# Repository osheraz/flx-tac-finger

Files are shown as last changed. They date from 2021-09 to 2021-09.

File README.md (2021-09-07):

# FlX Finger 

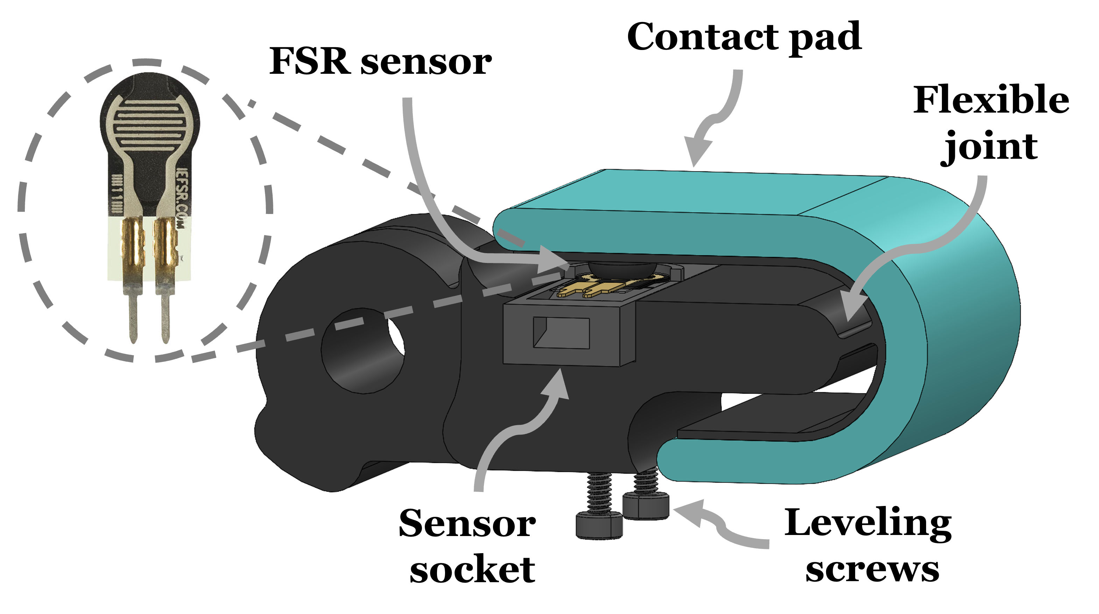
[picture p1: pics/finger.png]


This page provides instructions and design files for manufacturing the FlX finger.

## Background
FlX finger is a low-cost tactile finger. FlX finger is mostly fabricated through 3D printing and is based on the design of the distal finger link of the Model-T42 hand [1]. The FlX finger is composed of four parts seen in the figure above: finger body, contact pad, Force Sensitive Resistor (FSR) sensor and sensor socket. The finger body is connected to the contact pad solely through a flexible joint. In addition, the sensor socket with the FSR are positioned fixed to the finger body. At such configuration, the FSR is in contact with a small bulge on the back side of the contact pad.

## Force Sensitive Resistor (FSR)

FSR sensors are made of polymer films that vary their electrical resistance upon changing pressure on their surface. They are simple to use and low-cost. When an object is being pressed against the contact pad, the flexible joint and pad deform such that different contact locations across the pad provide different voltage. Pressure on the contact pad, therefore, provides voltage signals that embed information regarding the location and magnitude of contact. 

# Manufacture

## Required Materials
### Design files
1. FingerBody.stl
2. SensorSocket.stl

### Electrical
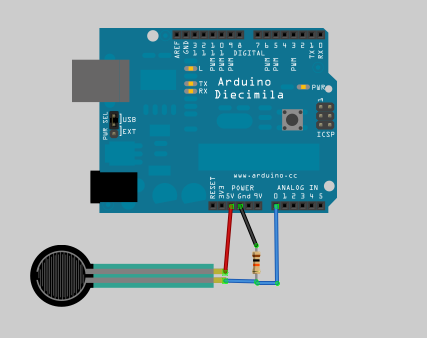
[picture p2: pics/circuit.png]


1. Arduino Uno\Nano or any equivalent board  
2. FSR 400 short by interlink electronics       
3. 4.7 kΩ resistor   
4. Wires
5. USB Cable
6. 2-Pin Female cable

### Chemicals
1.  Smooth-On Mold Star / Silicones, Inc. XP-565  or any related
2.  Ease Release 200 (not mandatory)

##  Procedure
All design files can be found in `cad` repo.\
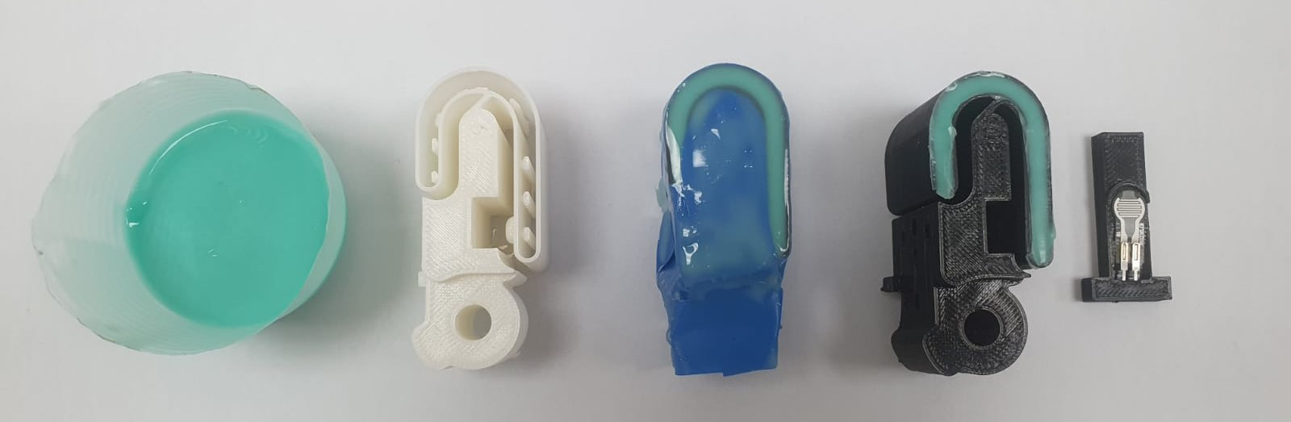
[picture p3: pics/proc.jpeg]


1. **Print parts**: Print `FingerBody.stl` and `SensorSocket.stl` in PLA using 3D printer. 
2. **Mix silicone** : Mix your silicone according to the manufacturer requirements, we used Smooth-On's silicone, which are easy to use without any vacuum degassing requirement. Mix enough Mold Star silicone ( equal amount A:B) to fill the shell of the `FingerBody`.
3. **Pour silicone**: slowly pour the silicone into the shell of the `FingerBody`. Let the silicone rest for approximtly 3 hours.
4.  **Wall removal**: Carefully remove the thin-walled molds of the  `FingerBody` using a small utility knife.
5. **Glue FSR**: Position& glue the FSR 400 short into the  `SensorSocket`.
6. **Attach insert**: Attach M2 heat insert at the bottom of the  `FingerBody` .
7.  **Wire**: Wire the FSR sensor to an analog pin of the Arduino Nano through a voltage divider of 4.7k$\Omega$ resistor.

# Test
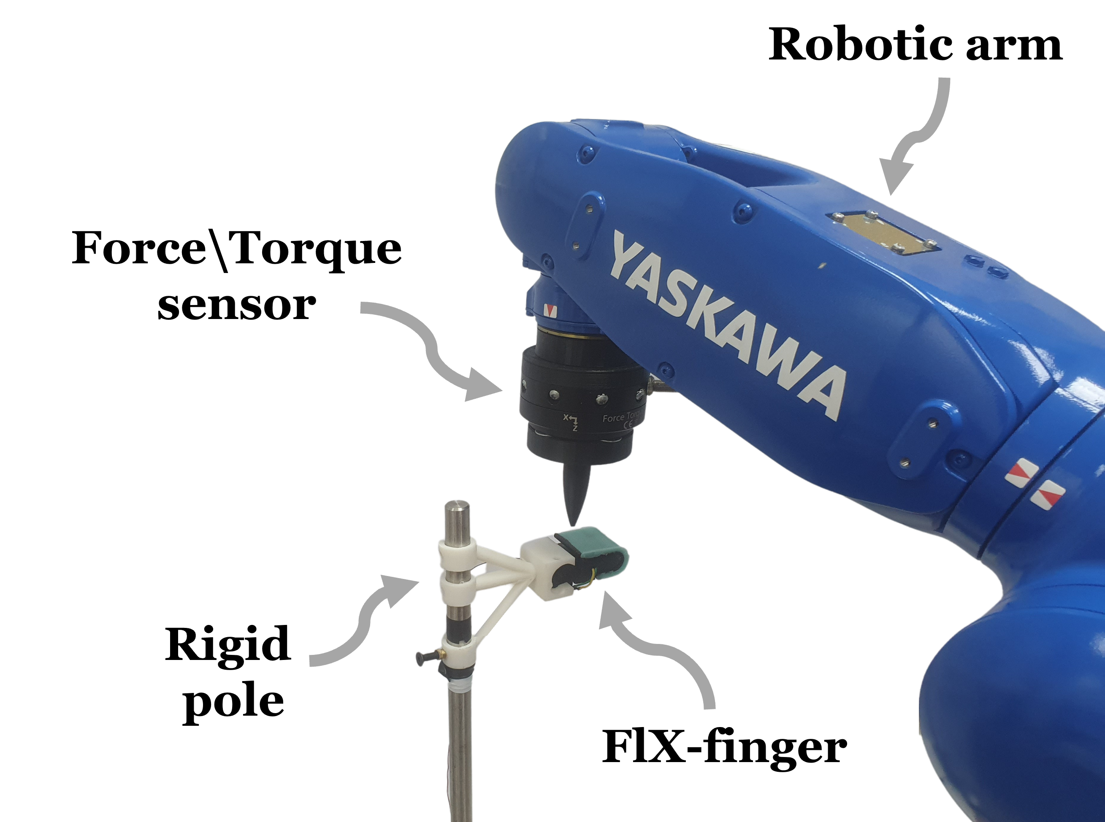
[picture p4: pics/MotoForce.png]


We tested the characteristic force distribution of the FlX finger, we have designed an experiment using a six degrees-of-freedom robotic arm equipped with a Force/Torque sensor and a rigid pole at its tip. During the experiment, the pole was pushed against the finger with predefined forces between 0-10 (N) and at 50 equal length locations along the contact pad. Results for FlX finger with initial voltage of 200 (mV) are seen in `test` repo. 
To acquire somewhat repeatability of measurements, leveling screws on the back side of the finger body are used to vary the height of the sensor socket and, thus, tune the initial voltage on the FSR. By standard, we tune the initial voltage with a weight of 100 grams directly placed on the contact pad when in an horizontal posture.

## Reference

[1] Ma, R., & Dollar, A. (2017). Yale OpenHand Project: Optimizing Open-Source Hand Designs for Ease of Fabrication and Adoption. _IEEE Robotics & Automation Magazine, 24_, 32-40.

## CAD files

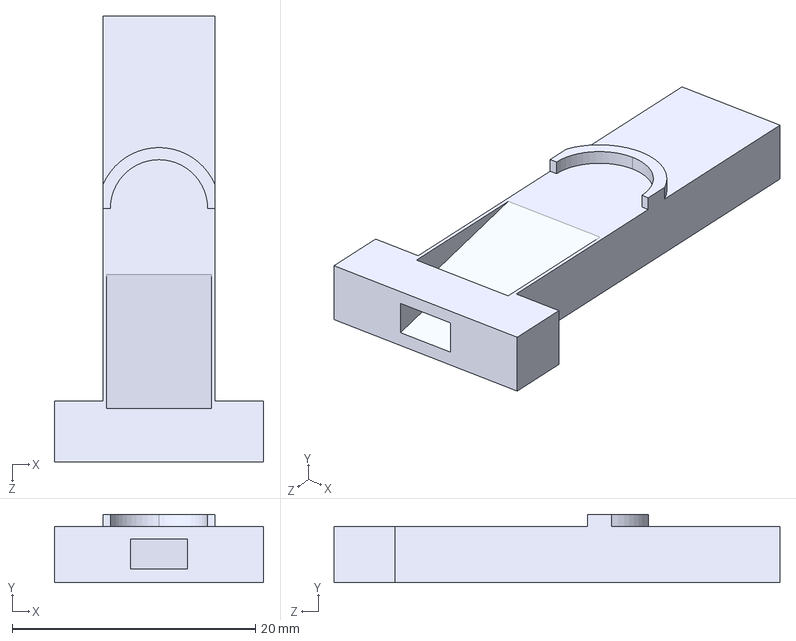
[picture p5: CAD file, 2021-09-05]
cads/SensorSocket.STEP
17.2 x 5.60 x 36.7 mm

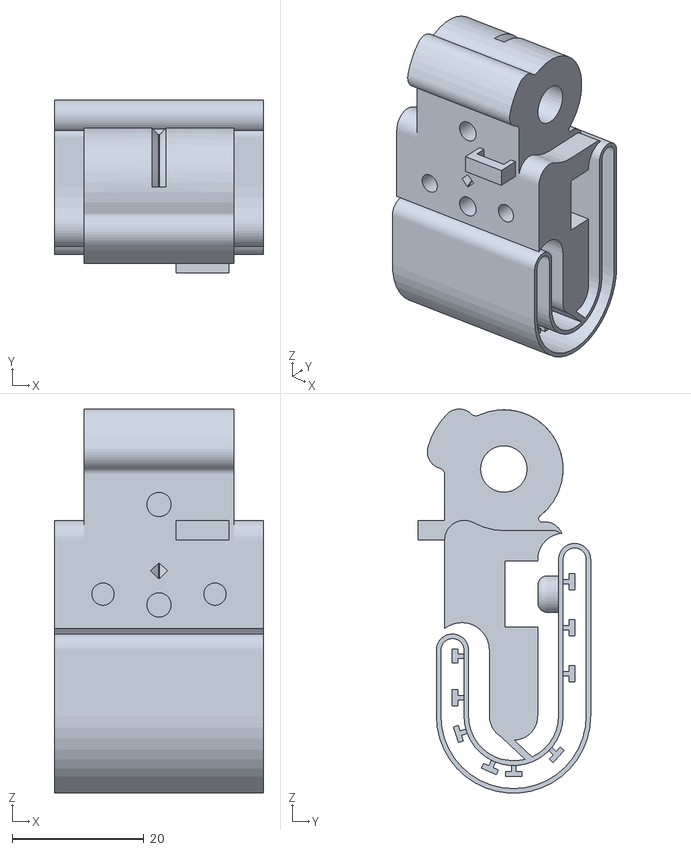
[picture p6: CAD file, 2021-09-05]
cads/FingerBody.STL
31.8 x 26.2 x 58.3

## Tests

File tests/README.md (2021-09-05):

# Signal distribution characterization
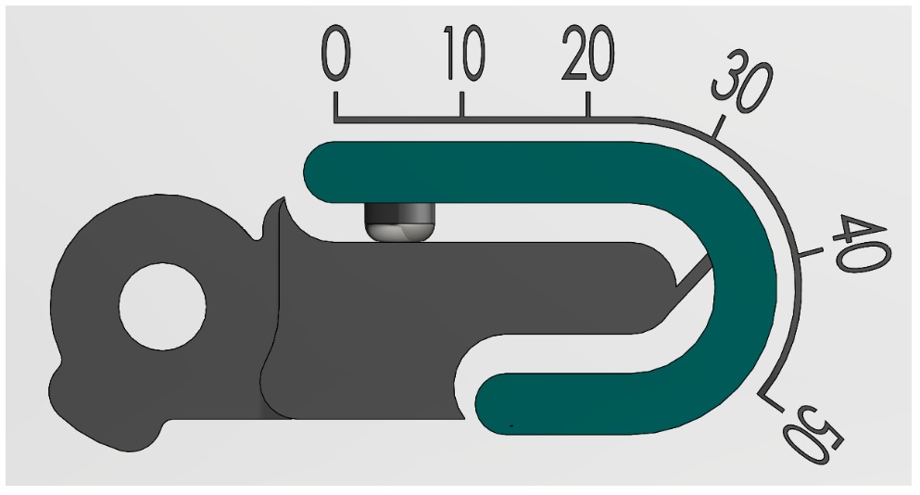
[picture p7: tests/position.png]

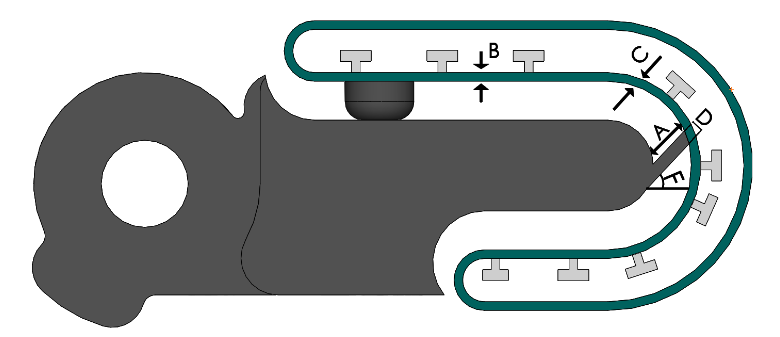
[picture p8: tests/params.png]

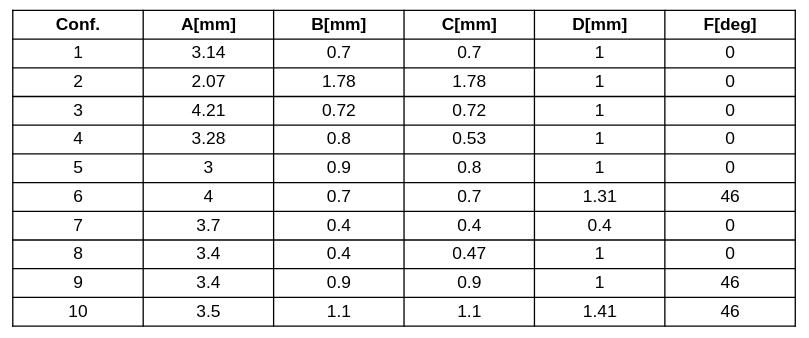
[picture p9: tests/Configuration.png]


This repo include the results of our experiment to characterize signal distribution on the FlX-finger.
We tested 10 design configurtions, where the parameter for each design can be seen in the Table above.
In each graph the grey area denotes the main working region during manipulation. When the contact is at the back of the finger, force is reduced on the FSR and the signal becomes negative (relative to the initial load).
